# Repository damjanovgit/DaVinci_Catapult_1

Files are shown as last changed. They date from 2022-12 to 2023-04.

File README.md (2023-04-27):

# DaVinci_Catapult_1

This project is done as practical part of subjects Computer electronics and Microcontroller systems in academic 2022/23 year, winter semester. 
For realisation, we had to design PCB with all components that we need to control stepper motors, which are used to position the catapult, then limit switches and lasers, and the final result, our catapult, is shown on picture below.
<p align="center">


## Connection instructions

### PCB power supply

First, we need to connect 12V supply to PCB, and we use proto-board as voltage source to input pins of LM317. Black wire is connected to the ground, and red one to +12V. (Note: on this proto-board is written that it gives +15V but in reality it is +12V voltage source, so it is recommended to always check all sources with multimeter).
<p align="center">


 ### Connecting Picket3 programmer to PCB
 
 For programming microcontroller we use Picket3 programmer, and it has 5 wires that need to be connected in proper way. At the pictures bellow we have shown Picket3 pinout and its connection to PCB.
 <p align="center">
 
 

 ### Stepper motor and laser connection
 Six stepper motors were used to operate the catapult. Of that number, two stepper motors are used to move the lasers, the remaining four are on the catapult itself.
 Connectors for stepper motors are marked with numbers 1, 2, 3 and 4 and they need to be placed as it is shown on the picture.
 Two connectors that are next to these are used for lasers, and it is important that whichever laser we connect next to connector 4 is considered as upper laser(goes on the left side of catapult).
 <p align="center">
 
 
 Power supply for lasers is connected as it is shown on next picture, wires for every laser go in pairs (+ -, + -). Next to this we connect limit switches(next 4 pins).
 
  <p align="center">
 
 
 ### Connecting to a computer
 
 For this, we use USB to UART converter that allows us to connect a device with a UART interface to a computer via a USB port.
  <p align="center">
 
 
When everything is propperly connected, it is necessary to enable the programming of the microcontroller on the board, and after this has been successfully completed, we can control the catapult. Controlling the catapult and lasers is done by entering appropriate characters into the serial communication terminal. The table below represents the commands with the corresponding characters and description.

| Command | Functionality |
| :---: | :---: |
| a | Laser 1 left rotation |
| d | Laser 1 right rotation |
| s | Stop laser 1 rotation |
| j | Laser 2 left rotation |
| l | Laser 2 right rotation |
| k | Stop laser 2 rotation |
| c | Calibration |
| f | Launch |
| p | Positioning of the catapult |
| b | Rotate catapult left |
| m | Rotate catapult right |
| n | Stop rotating |
| z | Tension management |
| u | Tension management |
| i | Firing |
| o | Firing |

Using the commands a, d, j and l we control the lasers by turning them left or right until we aim at the target. When the laser rays are intersected, it means that the target is aimed, and we stop their movement with the s and k commands. Once we have determined the position of the target, we use the p command to position the catapult so that it is ready for launch. Then, use command f to fire a cannonball. Using the b, m, n, z, u, i, o commands, manual control of all other motors is enabled for testing purposes.

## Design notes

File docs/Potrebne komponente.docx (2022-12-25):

LATCH FOR DRIVING STEPPER MOTORS:

X8

-catalog (https://eu.mouser.com/c/semiconductors/logic-ics/encoders-decoders-multiplexers-demultiplexers/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):

https://eu.mouser.com/ProductDetail/onsemi/MC74HC175ADG?qs=qg33o%252B8vzFoIlG2G0iHepQ%3D%3D

-datasheet (https://eu.mouser.com/datasheet/2/308/MC74HC175A_D-1811422.pdf)

DECODER 3/8

-catalog

https://eu.mouser.com/c/semiconductors/logic-ics/encoders-decoders-multiplexers-demultiplexers/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

-part

https://eu.mouser.com/ProductDetail/Texas-Instruments/SN74HCS237QDRQ1?qs=81r%252BiQLm7BRJlAHNZgIr4g%3D%3D

ULN2003

-part

https://eu.mouser.com/ProductDetail/STMicroelectronics/ULN2003D1013TR?qs=YnPipOpXm6FQ98RZGZk5Pg%3D%3D

CRYSTAL OSCILATOR

-catalog:

https://eu.mouser.com/c/passive-components/frequency-control-timing-devices/crystals/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

-potencijalno I ovaj

https://eu.mouser.com/ProductDetail/Wurth-Elektronik/830003151?qs=2WXlatMagcHisY7XHApyYg%3D%3D

-datasheet (https://eu.mouser.com/datasheet/2/445/830003156B-2005241.pdf)

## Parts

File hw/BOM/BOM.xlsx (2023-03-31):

Item | Qty | Reference(s) | Value | Mouser Part No. | Link to Mouser
1 | 1 | XTAL/S | 830003156B | 710-830003156B | https://eu.mouser.com/ProductDetail/Wurth-Elektronik/830003156B?qs=2WXlatMagcHnVMrUSWOG9g%3D%3D
2 | 1 | C7 | 10uF | 80-C0805C106K8R7210 | https://eu.mouser.com/ProductDetail/KEMET/C0805C106K8RAC7210?qs=qDynDzKJm89Noj94vfKrew%3D%3D
3 | 13 | C1, C2, C3,C5, C9, C12, C13, C14, C15, C16, C17, C18, C19 | 0.1uF | 80-C0805C104K5RACLR | https://eu.mouser.com/ProductDetail/KEMET/C0805C104K5RAC7411
4 | 1 | C20 | 100uF | 581-CM21X5R107M06AT | https://eu.mouser.com/ProductDetail/KYOCERA-AVX/CM21X5R107M06AT
5 | 1 | C4 | 1u | 80-C0805C105Z4V | https://eu.mouser.com/ProductDetail/KEMET/C0805C105Z4VACTU?qs=XSafd0xJmRINotKjOdb5hw%3D%3D
6 | 4 | C6, C8, C10, C11 | 47pF | 80-C0805C470J5GACLR | https://eu.mouser.com/ProductDetail/KEMET/C0805C470J5GAC7210?qs=wYAydIdPQphRIc65nI7ifw%3D%3D
7 | 1 | R3 | 240 | 603-RT0805BRD07240R | https://eu.mouser.com/ProductDetail/YAGEO/RT0805BRD07240RL?qs=aZCcseWLxnuOXuRNghjaKA%3D%3D
8 | 1 | R2 | 220 | 603-RT0805BRD07220RL | https://eu.mouser.com/ProductDetail/YAGEO/RT0805BRD07220RL?qs=%2Ff7pOCXLR5ctU4g2ONNN1A%3D%3D
9 | 2 | R11, R12 | 27 | 603-RT0805FRE0727RL | https://eu.mouser.com/ProductDetail/YAGEO/RT0805FRE0727RL?qs=4CyHz7GXqSiza0HQqKGx2Q%3D%3D
10 | 1 | R4 | 390 | 603-RT0805FRE07390RL | https://eu.mouser.com/ProductDetail/YAGEO/RT0805FRE07390RL?qs=%2FgLOArm3Wr4KJrVuTb07CQ%3D%3D
11 | 1 | IC2 | 317EMP | 863-LM317MADTRKG | https://eu.mouser.com/ProductDetail/onsemi/LM317MADTRKG?qs=2OtswVQKCOFlhMcZfF6npw%3D%3D
12 | 1 | IC1 |  | 579-PIC24FJ64GA002TI | https://eu.mouser.com/ProductDetail/Microchip-Technology/PIC24FJ64GA002T-I-SS?qs=Fllw7YelV393P08MHz84Bg%3D%3D
13 | 4 | IC9, IC10, IC11, IC12 | ULN2003D1013TR | 595-ULN2003AIDR | https://eu.mouser.com/ProductDetail/Texas-Instruments/ULN2003AIDR?qs=pbofycSusePLfAeFJ8tqkg%3D%3D
14 | 1 | IC13 | FT230XS-U | 895-FT230XS-U | https://eu.mouser.com/ProductDetail/FTDI/FT230XS-U?qs=Gp1Yz1mis3UZolxbXux7lw%3D%3D
15 | 6 | IC3, IC4, IC5, IC6, IC7, IC8 | MC74HC175ADG | 863-MC74HC175ADG | https://eu.mouser.com/ProductDetail/onsemi/MC74HC175ADG?qs=qg33o%252B8vzFoIlG2G0iHepQ%3D%3D
16 | 1 | U1 | Decoder/Demultiplexer | 771-74HC237D-Q100J | https://eu.mouser.com/ProductDetail/Nexperia/74HC237D-Q100J?qs=cbprxTG2Yq9x2EcO4aYbZA%3D%3D
17 | 1 | J1 | UJ2-BH-1-TH | 490-UJ2-BH-W2-TH | https://eu.mouser.com/ProductDetail/CUI-Devices/UJ2-BH-W2-TH?qs=5mqXD9RfOg2S8wXYHZgk9A%3D%3D
18 | 2 | PGEC_GP, PROG_VDD |  | 571-5-146280-3 | https://eu.mouser.com/ProductDetail/TE-Connectivity/5-146280-3?qs=bwpFY26eRVf7xnwkMZzVxA%3D%3D
19 | 10 | I2C_SPI, J8, J9, MOTOR1, MOTOR2, MOTOR3, MOTOR4, MOTOR5, MOTOR6, PROGRAMATOR |  | 649-68000-105HTLF | https://eu.mouser.com/ProductDetail/Amphenol-FCI/68000-105HTLF?qs=w%2Fv1CP2dgqrYgNyQVoiqDw%3D%3D
20 | 8 | R1, R5, R6, R7, R8, R9, R10, R13 | 10k | 603-RT0805BRD0710KL | https://eu.mouser.com/ProductDetail/YAGEO/RT0805BRD0710KL?qs=87%2Fgv35YuOdOfU%252BBkLDVxA%3D%3D
21 | 1 | GND PIN
22 | 1 | VDD PIN

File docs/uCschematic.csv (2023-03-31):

Part | Value | Device | Package | Description | ARROW_PART_NUMBER | ARROW_PRICE-STOCK | AVAILABILITY | DESCRIPTION | HEIGHT | MANUFACTURER_NAME | MANUFACTURER_PART_NUMBER | MF | MOUSER_PART_NUMBER | MOUSER_PRICE-STOCK | MOUSER_TESTING_PART_NUMBER | MOUSER_TESTING_PRICE-STOCK | MP | MPN | OC_FARNELL | OC_NEWARK | PACKAGE | POPULARITY | PRICE | PURCHASE-URL | SPICEMODEL | SPICEPREFIX
C1 | 100nF | C | C0805 | CAPACITOR, European symbol |  |  |  |  |  |  |  |  |  |  |  |  |  |  |  |  |  |  |  |  | NONE | C
C2 | 100nF | C | C0805 | CAPACITOR, European symbol |  |  |  |  |  |  |  |  |  |  |  |  |  |  |  |  |  |  |  |  | NONE | C
C3 | 100nF | C | C0805 | CAPACITOR, European symbol |  |  |  |  |  |  |  |  |  |  |  |  |  |  |  |  |  |  |  |  | NONE | C
C4 | 1u | C | C0805 | CAPACITOR, European symbol |  |  |  |  |  |  |  |  |  |  |  |  |  |  |  |  |  |  |  |  | NONE | C
C5 | 0.1u | C | C0805 | CAPACITOR, European symbol |  |  |  |  |  |  |  |  |  |  |  |  |  |  |  |  |  |  |  |  | NONE | C
C6 | 47pF | C | C0805 | CAPACITOR, European symbol |  |  |  |  |  |  |  |  |  |  |  |  |  |  |  |  |  |  |  |  | NONE | C
C7 | 10uF | C | C0805 | CAPACITOR, European symbol |  |  |  |  |  |  |  |  |  |  |  |  |  |  |  |  |  |  |  |  | NONE | C
C8 | 47pF | C | C0805 | CAPACITOR, European symbol |  |  |  |  |  |  |  |  |  |  |  |  |  |  |  |  |  |  |  |  | NONE | C
C9 | 0.1u | C | C0805 | CAPACITOR, European symbol |  |  |  |  |  |  |  |  |  |  |  |  |  |  |  |  |  |  |  |  | NONE | C
C10 | 47pF | C | C0805 | CAPACITOR, European symbol |  |  |  |  |  |  |  |  |  |  |  |  |  |  |  |  |  |  |  |  | NONE | C
C11 | 47pF | C | C0805 | CAPACITOR, European symbol |  |  |  |  |  |  |  |  |  |  |  |  |  |  |  |  |  |  |  |  | NONE | C
C12 | 0.1u | C | C0805 | CAPACITOR, European symbol |  |  |  |  |  |  |  |  |  |  |  |  |  |  |  |  |  |  |  |  | NONE | C
C13 | 0.1u | C | C0805 | CAPACITOR, European symbol |  |  |  |  |  |  |  |  |  |  |  |  |  |  |  |  |  |  |  |  | NONE | C
C14 | 0.1u | C | C0805 | CAPACITOR, European symbol |  |  |  |  |  |  |  |  |  |  |  |  |  |  |  |  |  |  |  |  | NONE | C
C15 | 0.1u | C | C0805 | CAPACITOR, European symbol |  |  |  |  |  |  |  |  |  |  |  |  |  |  |  |  |  |  |  |  | NONE | C
C16 | 0.1u | C | C0805 | CAPACITOR, European symbol |  |  |  |  |  |  |  |  |  |  |  |  |  |  |  |  |  |  |  |  | NONE | C
C17 | 0.1u | C | C0805 | CAPACITOR, European symbol |  |  |  |  |  |  |  |  |  |  |  |  |  |  |  |  |  |  |  |  | NONE | C
C18 | 0.1u | C | C0805 | CAPACITOR, European symbol |  |  |  |  |  |  |  |  |  |  |  |  |  |  |  |  |  |  |  |  | NONE | C
C19 | 0.1u | C | C0805 | CAPACITOR, European symbol |  |  |  |  |  |  |  |  |  |  |  |  |  |  |  |  |  |  |  |  | NONE | C
CAT_ANGLE | PIN1-2 | PIN1-2 | 62221 | CONN TAB FASTON BRASS .187 PCB |  |  |  |  |  |  |  | TYCO ELECTRONICS |  |  |  |  |  | 62221-1 | unknown | 16H2318
CAT_ROTATION | PIN1-2 | PIN1-2 | 62221 | CONN TAB FASTON BRASS .187 PCB |  |  |  |  |  |  |  | TYCO ELECTRONICS |  |  |  |  |  | 62221-1 | unknown | 16H2318
CS | PIN1-2 | PIN1-2 | 62221 | CONN TAB FASTON BRASS .187 PCB |  |  |  |  |  |  |  | TYCO ELECTRONICS |  |  |  |  |  | 62221-1 | unknown | 16H2318
GND | PIN1-2 | PIN1-2 | 62221 | CONN TAB FASTON BRASS .187 PCB |  |  |  |  |  |  |  | TYCO ELECTRONICS |  |  |  |  |  | 62221-1 | unknown | 16H2318
GND1 | PIN1-2 | PIN1-2 | 62221 | CONN TAB FASTON BRASS .187 PCB |  |  |  |  |  |  |  | TYCO ELECTRONICS |  |  |  |  |  | 62221-1 | unknown | 16H2318
GND_CAT_ANGLE | PIN1-2 | PIN1-2 | 62221 | CONN TAB FASTON BRASS .187 PCB |  |  |  |  |  |  |  | TYCO ELECTRONICS |  |  |  |  |  | 62221-1 | unknown | 16H2318
GND_CAT_ROTATION | PIN1-2 | PIN1-2 | 62221 | CONN TAB FASTON BRASS .187 PCB |  |  |  |  |  |  |  | TYCO ELECTRONICS |  |  |  |  |  | 62221-1 | unknown | 16H2318
GND_GP_1 | PIN1-2 | PIN1-2 | 62221 | CONN TAB FASTON BRASS .187 PCB |  |  |  |  |  |  |  | TYCO ELECTRONICS |  |  |  |  |  | 62221-1 | unknown | 16H2318
GND_GP_LASER1 | PIN1-2 | PIN1-2 | 62221 | CONN TAB FASTON BRASS .187 PCB |  |  |  |  |  |  |  | TYCO ELECTRONICS |  |  |  |  |  | 62221-1 | unknown | 16H2318
GND_GP_LASER2 | PIN1-2 | PIN1-2 | 62221 | CONN TAB FASTON BRASS .187 PCB |  |  |  |  |  |  |  | TYCO ELECTRONICS |  |  |  |  |  | 62221-1 | unknown | 16H2318
GND_SM1 | PIN1-2 | PIN1-2 | 62221 | CONN TAB FASTON BRASS .187 PCB |  |  |  |  |  |  |  | TYCO ELECTRONICS |  |  |  |  |  | 62221-1 | unknown | 16H2318
GND_SM2 | PIN1-2 | PIN1-2 | 62221 | CONN TAB FASTON BRASS .187 PCB |  |  |  |  |  |  |  | TYCO ELECTRONICS |  |  |  |  |  | 62221-1 | unknown | 16H2318
GND_SM3 | PIN1-2 | PIN1-2 | 62221 | CONN TAB FASTON BRASS .187 PCB |  |  |  |  |  |  |  | TYCO ELECTRONICS |  |  |  |  |  | 62221-1 | unknown | 16H2318
GND_SM4 | PIN1-2 | PIN1-2 | 62221 | CONN TAB FASTON BRASS .187 PCB |  |  |  |  |  |  |  | TYCO ELECTRONICS |  |  |  |  |  | 62221-1 | unknown | 16H2318
GND_SM5 | PIN1-2 | PIN1-2 | 62221 | CONN TAB FASTON BRASS .187 PCB |  |  |  |  |  |  |  | TYCO ELECTRONICS |  |  |  |  |  | 62221-1 | unknown | 16H2318
GND_SM6 | PIN1-2 | PIN1-2 | 62221 | CONN TAB FASTON BRASS .187 PCB |  |  |  |  |  |  |  | TYCO ELECTRONICS |  |  |  |  |  | 62221-1 | unknown | 16H2318
GND_SPI/I2C | PIN1-2 | PIN1-2 | 62221 | CONN TAB FASTON BRASS .187 PCB |  |  |  |  |  |  |  | TYCO ELECTRONICS |  |  |  |  |  | 62221-1 | unknown | 16H2318
GP | PIN1-2 | PIN1-2 | 62221 | CONN TAB FASTON BRASS .187 PCB |  |  |  |  |  |  |  | TYCO ELECTRONICS |  |  |  |  |  | 62221-1 | unknown | 16H2318
GP_1 | PIN1-2 | PIN1-2 | 62221 | CONN TAB FASTON BRASS .187 PCB |  |  |  |  |  |  |  | TYCO ELECTRONICS |  |  |  |  |  | 62221-1 | unknown | 16H2318
GP_LASER1 | PIN1-2 | PIN1-2 | 62221 | CONN TAB FASTON BRASS .187 PCB |  |  |  |  |  |  |  | TYCO ELECTRONICS |  |  |  |  |  | 62221-1 | unknown | 16H2318
GP_LASER2 | PIN1-2 | PIN1-2 | 62221 | CONN TAB FASTON BRASS .187 PCB |  |  |  |  |  |  |  | TYCO ELECTRONICS |  |  |  |  |  | 62221-1 | unknown | 16H2318
IC1 | PIC24FJXXGA002/SO | PIC24FJXXGA002/SO | SO28W | PIC24FJxxGA002
IC2 | 317EMP | 317EMP | SOT223 | Positive VOLTAGE REGULATOR
IC3 | MC74HC175ADG | MC74HC175ADG | SOIC127P600X175-16N | ON Semiconductor MC74HC175ADG, D Type Flip Flop, LSTTL, 2 6 V, 16-Pin SOIC |  |  |  | ON Semiconductor MC74HC175ADG, D Type Flip Flop, LSTTL, 2 6 V, 16-Pin SOIC | 1.75mm | onsemi | MC74HC175ADG |  | 863-MC74HC175ADG | https://www.mouser.co.uk/ProductDetail/onsemi/MC74HC175ADG?qs=qg33o%252B8vzFoIlG2G0iHepQ%3D%3D
IC4 | MC74HC175ADG | MC74HC175ADG | SOIC127P600X175-16N | ON Semiconductor MC74HC175ADG, D Type Flip Flop, LSTTL, 2 6 V, 16-Pin SOIC |  |  |  | ON Semiconductor MC74HC175ADG, D Type Flip Flop, LSTTL, 2 6 V, 16-Pin SOIC | 1.75mm | onsemi | MC74HC175ADG |  | 863-MC74HC175ADG | https://www.mouser.co.uk/ProductDetail/onsemi/MC74HC175ADG?qs=qg33o%252B8vzFoIlG2G0iHepQ%3D%3D
IC5 | MC74HC175ADG | MC74HC175ADG | SOIC127P600X175-16N | ON Semiconductor MC74HC175ADG, D Type Flip Flop, LSTTL, 2 6 V, 16-Pin SOIC |  |  |  | ON Semiconductor MC74HC175ADG, D Type Flip Flop, LSTTL, 2 6 V, 16-Pin SOIC | 1.75mm | onsemi | MC74HC175ADG |  | 863-MC74HC175ADG | https://www.mouser.co.uk/ProductDetail/onsemi/MC74HC175ADG?qs=qg33o%252B8vzFoIlG2G0iHepQ%3D%3D
IC6 | MC74HC175ADG | MC74HC175ADG | SOIC127P600X175-16N | ON Semiconductor MC74HC175ADG, D Type Flip Flop, LSTTL, 2 6 V, 16-Pin SOIC |  |  |  | ON Semiconductor MC74HC175ADG, D Type Flip Flop, LSTTL, 2 6 V, 16-Pin SOIC | 1.75mm | onsemi | MC74HC175ADG |  | 863-MC74HC175ADG | https://www.mouser.co.uk/ProductDetail/onsemi/MC74HC175ADG?qs=qg33o%252B8vzFoIlG2G0iHepQ%3D%3D
IC7 | MC74HC175ADG | MC74HC175ADG | SOIC127P600X175-16N | ON Semiconductor MC74HC175ADG, D Type Flip Flop, LSTTL, 2 6 V, 16-Pin SOIC |  |  |  | ON Semiconductor MC74HC175ADG, D Type Flip Flop, LSTTL, 2 6 V, 16-Pin SOIC | 1.75mm | onsemi | MC74HC175ADG |  | 863-MC74HC175ADG | https://www.mouser.co.uk/ProductDetail/onsemi/MC74HC175ADG?qs=qg33o%252B8vzFoIlG2G0iHepQ%3D%3D
IC8 | MC74HC175ADG | MC74HC175ADG | SOIC127P600X175-16N | ON Semiconductor MC74HC175ADG, D Type Flip Flop, LSTTL, 2 6 V, 16-Pin SOIC |  |  |  | ON Semiconductor MC74HC175ADG, D Type Flip Flop, LSTTL, 2 6 V, 16-Pin SOIC | 1.75mm | onsemi | MC74HC175ADG |  | 863-MC74HC175ADG | https://www.mouser.co.uk/ProductDetail/onsemi/MC74HC175ADG?qs=qg33o%252B8vzFoIlG2G0iHepQ%3D%3D
IC9 | ULN2003D1013TR | ULN2003D1013TR | SOIC127P600X175-16N | ULN2003D1013TR, Darlington Transistor Array, NPN 0.5A 50V, Array 7 HFE:1000, 16-Pin, SO |  |  |  | ULN2003D1013TR, Darlington Transistor Array, NPN 0.5A 50V, Array 7 HFE:1000, 16-Pin, SO | 1.75mm | STMicroelectronics | ULN2003D1013TR |  | 511-ULN2003D1013TR | https://www.mouser.co.uk/ProductDetail/STMicroelectronics/ULN2003D1013TR?qs=YnPipOpXm6FQ98RZGZk5Pg%3D%3D
IC10 | ULN2003D1013TR | ULN2003D1013TR | SOIC127P600X175-16N | ULN2003D1013TR, Darlington Transistor Array, NPN 0.5A 50V, Array 7 HFE:1000, 16-Pin, SO |  |  |  | ULN2003D1013TR, Darlington Transistor Array, NPN 0.5A 50V, Array 7 HFE:1000, 16-Pin, SO | 1.75mm | STMicroelectronics | ULN2003D1013TR |  | 511-ULN2003D1013TR | https://www.mouser.co.uk/ProductDetail/STMicroelectronics/ULN2003D1013TR?qs=YnPipOpXm6FQ98RZGZk5Pg%3D%3D
IC11 | ULN2003D1013TR | ULN2003D1013TR | SOIC127P600X175-16N | ULN2003D1013TR, Darlington Transistor Array, NPN 0.5A 50V, Array 7 HFE:1000, 16-Pin, SO |  |  |  | ULN2003D1013TR, Darlington Transistor Array, NPN 0.5A 50V, Array 7 HFE:1000, 16-Pin, SO | 1.75mm | STMicroelectronics | ULN2003D1013TR |  | 511-ULN2003D1013TR | https://www.mouser.co.uk/ProductDetail/STMicroelectronics/ULN2003D1013TR?qs=YnPipOpXm6FQ98RZGZk5Pg%3D%3D
IC12 | ULN2003D1013TR | ULN2003D1013TR | SOIC127P600X175-16N | ULN2003D1013TR, Darlington Transistor Array, NPN 0.5A 50V, Array 7 HFE:1000, 16-Pin, SO |  |  |  | ULN2003D1013TR, Darlington Transistor Array, NPN 0.5A 50V, Array 7 HFE:1000, 16-Pin, SO | 1.75mm | STMicroelectronics | ULN2003D1013TR |  | 511-ULN2003D1013TR | https://www.mouser.co.uk/ProductDetail/STMicroelectronics/ULN2003D1013TR?qs=YnPipOpXm6FQ98RZGZk5Pg%3D%3D
IC13 | FT230XS-U | FT230XS-U | SOP64P599X175-16N | USB Interface IC USB to Basic Serial UART IC SSOP-16 | FT230XS-U | https://www.arrow.com/en/products/ft230xs-u/ftdi-chip |  | USB Interface IC USB to Basic Serial UART IC SSOP-16 | 1.753mm | FTDI Chip | FT230XS-U |  | 895-FT230XS-U | https://www.mouser.co.uk/ProductDetail/FTDI/FT230XS-U?qs=Gp1Yz1mis3UZolxbXux7lw%3D%3D
J1 | USB3075-30-A | USB3075-30-A | USB307530A | GCT (GLOBAL CONNECTOR TECHNOLOGY) - USB3075-30-A - USB Connector, Micro USB Type B, USB 2.0, Receptacle, 5 Ways, Surface Mount, Right Angle |  |  |  | GCT (GLOBAL CONNECTOR TECHNOLOGY) - USB3075-30-A - USB Connector, Micro USB Type B, USB 2.0, Receptacle, 5 Ways, Surface Mount, Right Angle | 2.7mm | GCT (GLOBAL CONNECTOR TECHNOLOGY) | USB3075-30-A |  | 640-USB3075-30-A | https://www.mouser.co.uk/ProductDetail/GCT/USB3075-30-A?qs=KUoIvG%2F9IlbGMJplbp1ybA%3D%3D
MCLR | PIN1-2 | PIN1-2 | 62221 | CONN TAB FASTON BRASS .187 PCB |  |  |  |  |  |  |  | TYCO ELECTRONICS |  |  |  |  |  | 62221-1 | unknown | 16H2318
MISO | PIN1-2 | PIN1-2 | 62221 | CONN TAB FASTON BRASS .187 PCB |  |  |  |  |  |  |  | TYCO ELECTRONICS |  |  |  |  |  | 62221-1 | unknown | 16H2318
PGEC | PIN1-2 | PIN1-2 | 62221 | CONN TAB FASTON BRASS .187 PCB |  |  |  |  |  |  |  | TYCO ELECTRONICS |  |  |  |  |  | 62221-1 | unknown | 16H2318
PGEC/GP | PIN1-2 | PIN1-2 | 62221 | CONN TAB FASTON BRASS .187 PCB |  |  |  |  |  |  |  | TYCO ELECTRONICS |  |  |  |  |  | 62221-1 | unknown | 16H2318
PGEC_PROG | PIN1-2 | PIN1-2 | 62221 | CONN TAB FASTON BRASS .187 PCB |  |  |  |  |  |  |  | TYCO ELECTRONICS |  |  |  |  |  | 62221-1 | unknown | 16H2318
PGED | PIN1-2 | PIN1-2 | 62221 | CONN TAB FASTON BRASS .187 PCB |  |  |  |  |  |  |  | TYCO ELECTRONICS |  |  |  |  |  | 62221-1 | unknown | 16H2318
Q1 |  | XTAL/S | QS | CRYSTAL |  |  |  |  |  |  |  |  |  |  |  |  |  |  |  |  |  | 59
R1 | 10k | R | R0805 | RESISTOR, European symbol |  |  |  |  |  |  |  |  |  |  |  |  |  |  |  |  |  |  |  |  | NONE | R
R2 | 220 | R | R0805 | RESISTOR, European symbol |  |  |  |  |  |  |  |  |  |  |  |  |  |  |  |  |  |  |  |  | NONE | R
R3 | 240 | R | R0805 | RESISTOR, European symbol |  |  |  |  |  |  |  |  |  |  |  |  |  |  |  |  |  |  |  |  | NONE | R
R4 | 390 | R | R0805 | RESISTOR, European symbol |  |  |  |  |  |  |  |  |  |  |  |  |  |  |  |  |  |  |  |  | NONE | R
R5 | 10k | R | R0805 | RESISTOR, European symbol |  |  |  |  |  |  |  |  |  |  |  |  |  |  |  |  |  |  |  |  | NONE | R
R6 | 10k | R | R0805 | RESISTOR, European symbol |  |  |  |  |  |  |  |  |  |  |  |  |  |  |  |  |  |  |  |  | NONE | R
R7 | 10k | R | R0805 | RESISTOR, European symbol |  |  |  |  |  |  |  |  |  |  |  |  |  |  |  |  |  |  |  |  | NONE | R
R8 | 10k | R | R0805 | RESISTOR, European symbol |  |  |  |  |  |  |  |  |  |  |  |  |  |  |  |  |  |  |  |  | NONE | R
R9 | 10k | R | R0805 | RESISTOR, European symbol |  |  |  |  |  |  |  |  |  |  |  |  |  |  |  |  |  |  |  |  | NONE | R
R10 | 10k | R | R0805 | RESISTOR, European symbol |  |  |  |  |  |  |  |  |  |  |  |  |  |  |  |  |  |  |  |  | NONE | R
R11 | 27 | R-EU_R0805 | R0805 | RESISTOR, European symbol |  |  |  |  |  |  |  |  |  |  |  |  |  |  |  |  |  | 86 |  |  |  | R
R12 | 27 | R-EU_R0805 | R0805 | RESISTOR, European symbol |  |  |  |  |  |  |  |  |  |  |  |  |  |  |  |  |  | 86 |  |  |  | R
SCLK/SCL | PIN1-2 | PIN1-2 | 62221 | CONN TAB FASTON BRASS .187 PCB |  |  |  |  |  |  |  | TYCO ELECTRONICS |  |  |  |  |  | 62221-1 | unknown | 16H2318
SDA/MOSI | PIN1-2 | PIN1-2 | 62221 | CONN TAB FASTON BRASS .187 PCB |  |  |  |  |  |  |  | TYCO ELECTRONICS |  |  |  |  |  | 62221-1 | unknown | 16H2318
SM11 | PIN1-2 | PIN1-2 | 62221 | CONN TAB FASTON BRASS .187 PCB |  |  |  |  |  |  |  | TYCO ELECTRONICS |  |  |  |  |  | 62221-1 | unknown | 16H2318
SM12 | PIN1-2 | PIN1-2 | 62221 | CONN TAB FASTON BRASS .187 PCB |  |  |  |  |  |  |  | TYCO ELECTRONICS |  |  |  |  |  | 62221-1 | unknown | 16H2318
SM13 | PIN1-2 | PIN1-2 | 62221 | CONN TAB FASTON BRASS .187 PCB |  |  |  |  |  |  |  | TYCO ELECTRONICS |  |  |  |  |  | 62221-1 | unknown | 16H2318
SM14 | PIN1-2 | PIN1-2 | 62221 | CONN TAB FASTON BRASS .187 PCB |  |  |  |  |  |  |  | TYCO ELECTRONICS |  |  |  |  |  | 62221-1 | unknown | 16H2318
SM21 | PIN1-2 | PIN1-2 | 62221 | CONN TAB FASTON BRASS .187 PCB |  |  |  |  |  |  |  | TYCO ELECTRONICS |  |  |  |  |  | 62221-1 | unknown | 16H2318
SM22 | PIN1-2 | PIN1-2 | 62221 | CONN TAB FASTON BRASS .187 PCB |  |  |  |  |  |  |  | TYCO ELECTRONICS |  |  |  |  |  | 62221-1 | unknown | 16H2318
SM23 | PIN1-2 | PIN1-2 | 62221 | CONN TAB FASTON BRASS .187 PCB |  |  |  |  |  |  |  | TYCO ELECTRONICS |  |  |  |  |  | 62221-1 | unknown | 16H2318
SM24 | PIN1-2 | PIN1-2 | 62221 | CONN TAB FASTON BRASS .187 PCB |  |  |  |  |  |  |  | TYCO ELECTRONICS |  |  |  |  |  | 62221-1 | unknown | 16H2318
SM31 | PIN1-2 | PIN1-2 | 62221 | CONN TAB FASTON BRASS .187 PCB |  |  |  |  |  |  |  | TYCO ELECTRONICS |  |  |  |  |  | 62221-1 | unknown | 16H2318
SM32 | PIN1-2 | PIN1-2 | 62221 | CONN TAB FASTON BRASS .187 PCB |  |  |  |  |  |  |  | TYCO ELECTRONICS |  |  |  |  |  | 62221-1 | unknown | 16H2318
SM33 | PIN1-2 | PIN1-2 | 62221 | CONN TAB FASTON BRASS .187 PCB |  |  |  |  |  |  |  | TYCO ELECTRONICS |  |  |  |  |  | 62221-1 | unknown | 16H2318
SM34 | PIN1-2 | PIN1-2 | 62221 | CONN TAB FASTON BRASS .187 PCB |  |  |  |  |  |  |  | TYCO ELECTRONICS |  |  |  |  |  | 62221-1 | unknown | 16H2318
SM41 | PIN1-2 | PIN1-2 | 62221 | CONN TAB FASTON BRASS .187 PCB |  |  |  |  |  |  |  | TYCO ELECTRONICS |  |  |  |  |  | 62221-1 | unknown | 16H2318
SM42 | PIN1-2 | PIN1-2 | 62221 | CONN TAB FASTON BRASS .187 PCB |  |  |  |  |  |  |  | TYCO ELECTRONICS |  |  |  |  |  | 62221-1 | unknown | 16H2318
SM43 | PIN1-2 | PIN1-2 | 62221 | CONN TAB FASTON BRASS .187 PCB |  |  |  |  |  |  |  | TYCO ELECTRONICS |  |  |  |  |  | 62221-1 | unknown | 16H2318
SM44 | PIN1-2 | PIN1-2 | 62221 | CONN TAB FASTON BRASS .187 PCB |  |  |  |  |  |  |  | TYCO ELECTRONICS |  |  |  |  |  | 62221-1 | unknown | 16H2318
SM51 | PIN1-2 | PIN1-2 | 62221 | CONN TAB FASTON BRASS .187 PCB |  |  |  |  |  |  |  | TYCO ELECTRONICS |  |  |  |  |  | 62221-1 | unknown | 16H2318
SM52 | PIN1-2 | PIN1-2 | 62221 | CONN TAB FASTON BRASS .187 PCB |  |  |  |  |  |  |  | TYCO ELECTRONICS |  |  |  |  |  | 62221-1 | unknown | 16H2318
SM53 | PIN1-2 | PIN1-2 | 62221 | CONN TAB FASTON BRASS .187 PCB |  |  |  |  |  |  |  | TYCO ELECTRONICS |  |  |  |  |  | 62221-1 | unknown | 16H2318
SM54 | PIN1-2 | PIN1-2 | 62221 | CONN TAB FASTON BRASS .187 PCB |  |  |  |  |  |  |  | TYCO ELECTRONICS |  |  |  |  |  | 62221-1 | unknown | 16H2318
SM61 | PIN1-2 | PIN1-2 | 62221 | CONN TAB FASTON BRASS .187 PCB |  |  |  |  |  |  |  | TYCO ELECTRONICS |  |  |  |  |  | 62221-1 | unknown | 16H2318
SM62 | PIN1-2 | PIN1-2 | 62221 | CONN TAB FASTON BRASS .187 PCB |  |  |  |  |  |  |  | TYCO ELECTRONICS |  |  |  |  |  | 62221-1 | unknown | 16H2318
SM63 | PIN1-2 | PIN1-2 | 62221 | CONN TAB FASTON BRASS .187 PCB |  |  |  |  |  |  |  | TYCO ELECTRONICS |  |  |  |  |  | 62221-1 | unknown | 16H2318
SM64 | PIN1-2 | PIN1-2 | 62221 | CONN TAB FASTON BRASS .187 PCB |  |  |  |  |  |  |  | TYCO ELECTRONICS |  |  |  |  |  | 62221-1 | unknown | 16H2318
U1 | 74HC237D-Q100J | 74HC237D-Q100J | SOIC127P600X175-16N | None Check availability |  |  | In Stock | Decoder/Demultiplexer 1 x 3:8 16-SO |  |  |  | Nexperia USA Inc. |  |  |  |  | 74HC237D-Q100J |  |  |  | SOIC-16 Nexperia USA |  | None | https://pricing.snapeda.com/search/part/74HC237D-Q100J/?ref=eda
VDD | 12V | PIN1-2 | 62221 | CONN TAB FASTON BRASS .187 PCB |  |  |  |  |  |  |  | TYCO ELECTRONICS |  |  |  |  |  | 62221-1 | unknown | 16H2318
VDD_3.3 | PIN1-2 | PIN1-2 | 62221 | CONN TAB FASTON BRASS .187 PCB |  |  |  |  |  |  |  | TYCO ELECTRONICS |  |  |  |  |  | 62221-1 | unknown | 16H2318
VDD_PROG | PIN1-2 | PIN1-2 | 62221 | CONN TAB FASTON BRASS .187 PCB |  |  |  |  |  |  |  | TYCO ELECTRONICS |  |  |  |  |  | 62221-1 | unknown | 16H2318
VDD_PROG1 | PIN1-2 | PIN1-2 | 62221 | CONN TAB FASTON BRASS .187 PCB |  |  |  |  |  |  |  | TYCO ELECTRONICS |  |  |  |  |  | 62221-1 | unknown | 16H2318
VDD_UC | PIN1-2 | PIN1-2 | 62221 | CONN TAB FASTON BRASS .187 PCB |  |  |  |  |  |  |  | TYCO ELECTRONICS |  |  |  |  |  | 62221-1 | unknown | 16H2318

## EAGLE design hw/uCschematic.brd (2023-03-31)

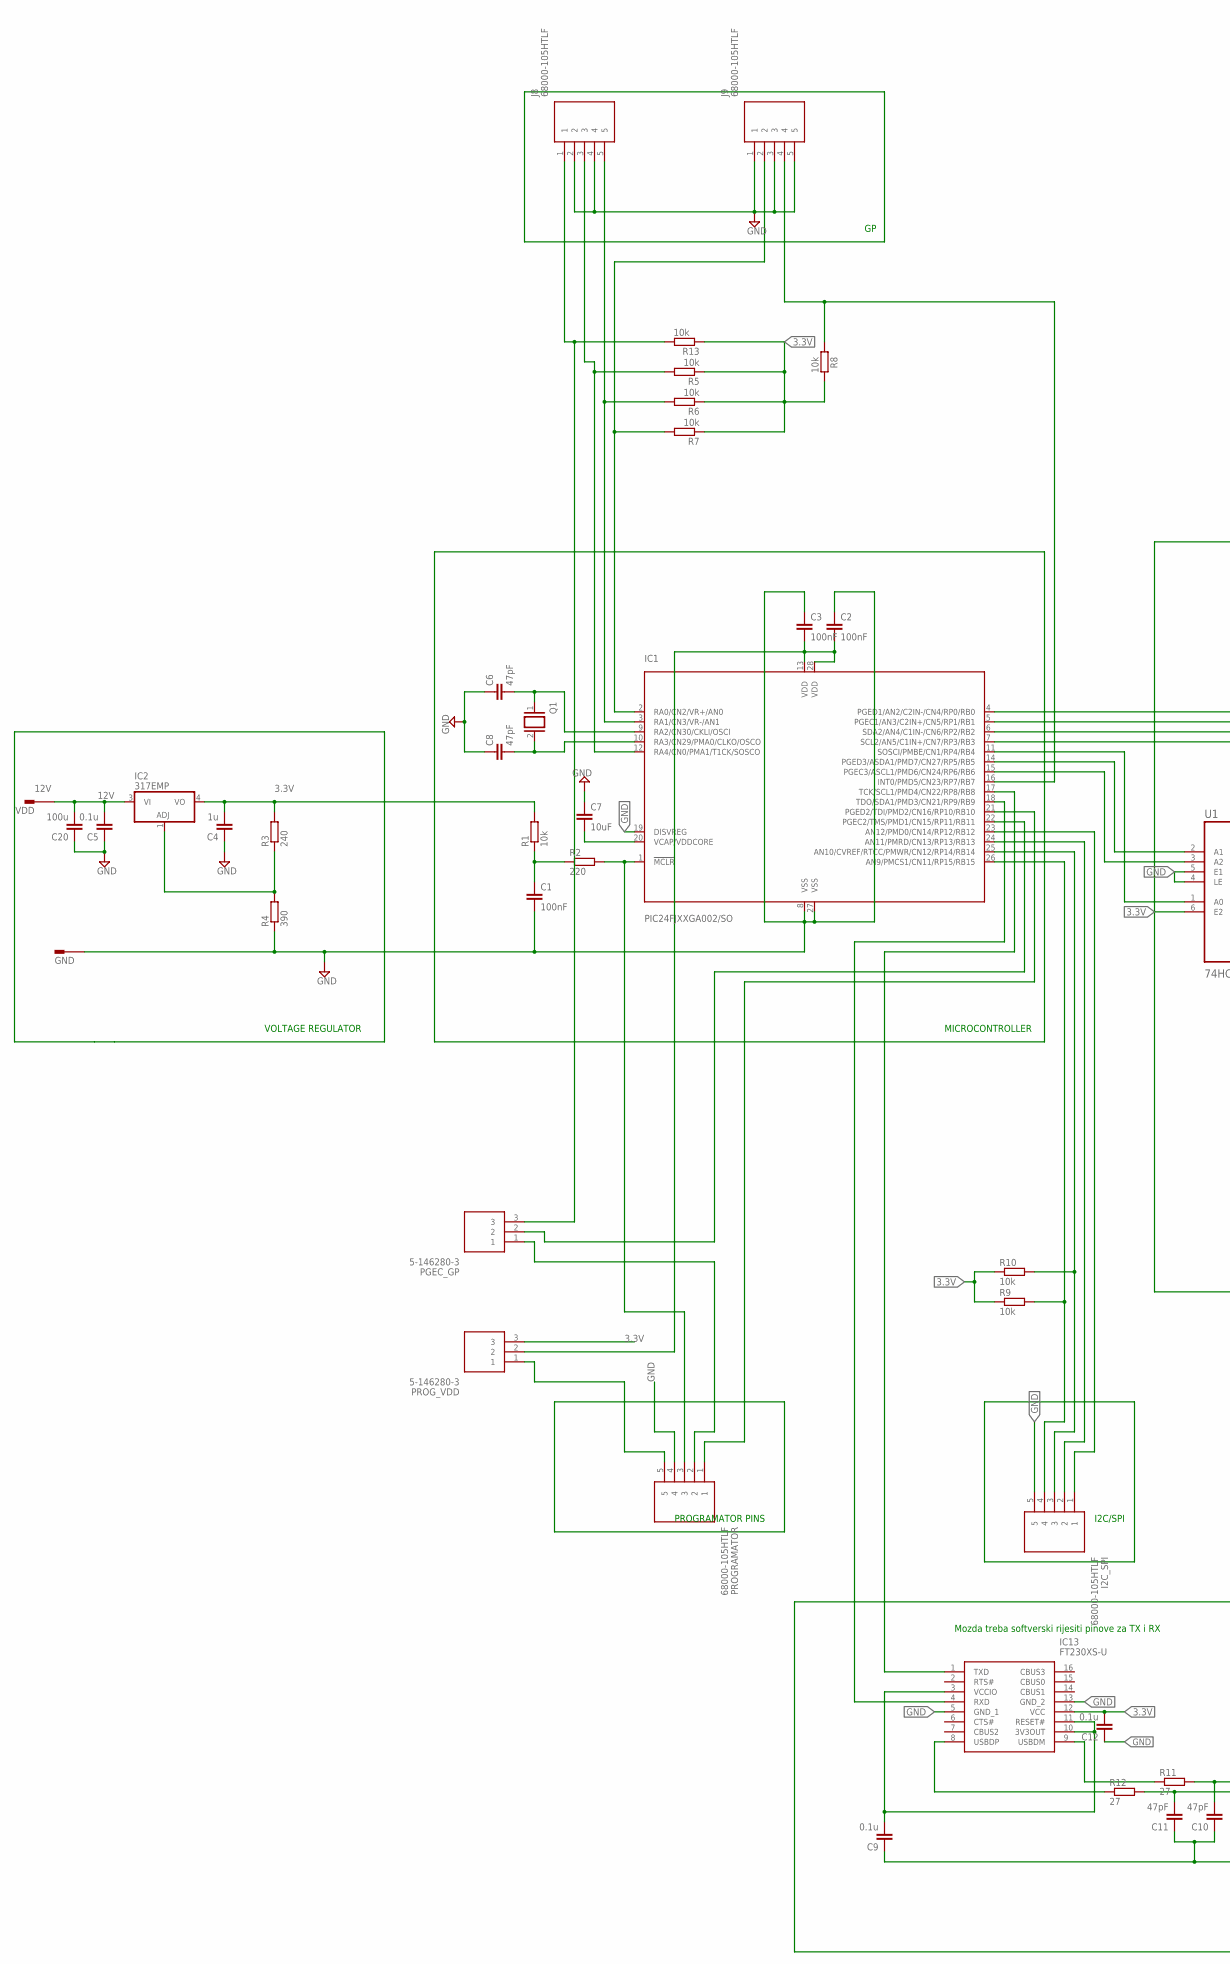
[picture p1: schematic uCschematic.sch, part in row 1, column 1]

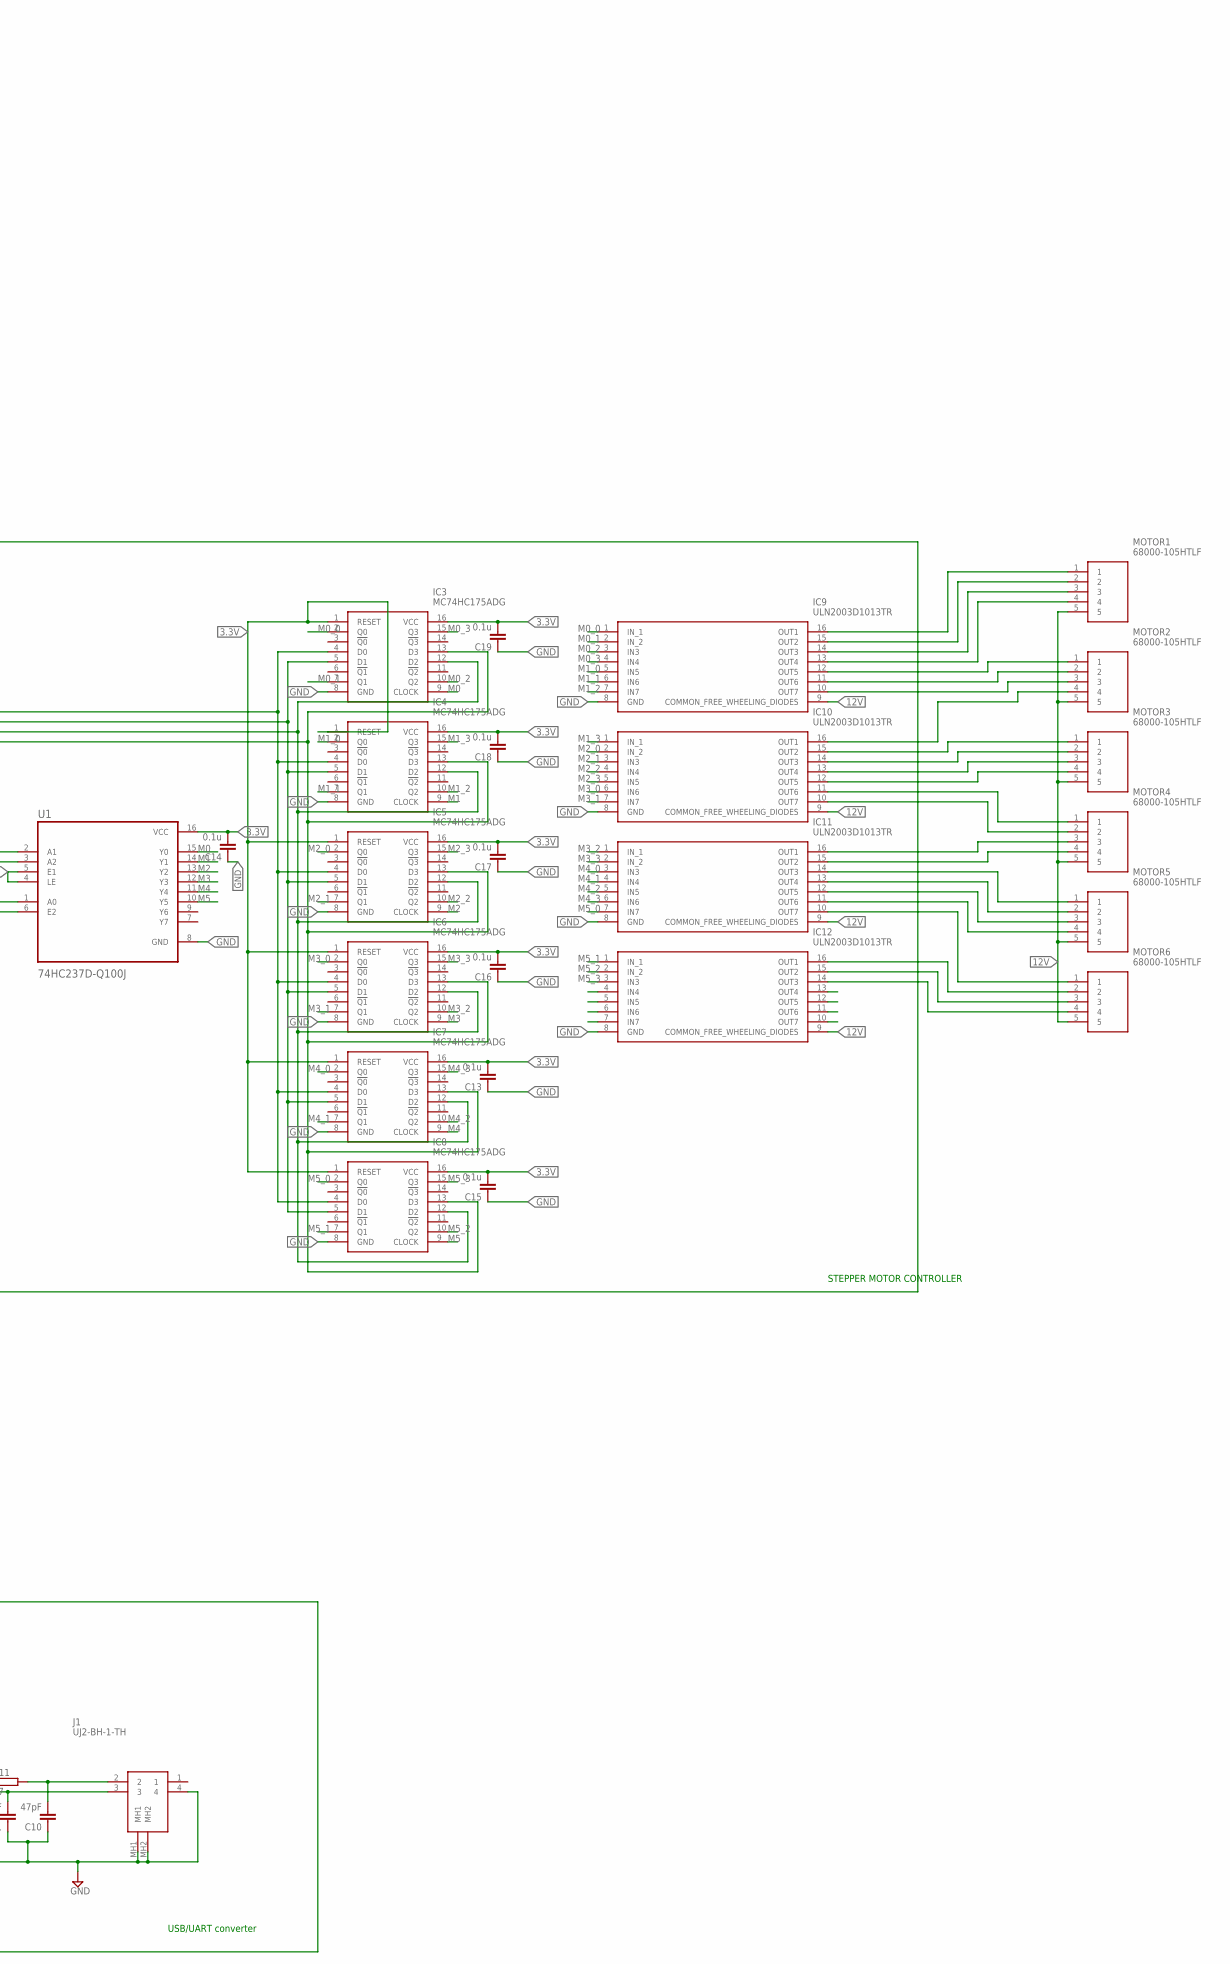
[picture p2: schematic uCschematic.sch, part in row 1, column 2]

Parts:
C1, C2, C3: 100nF; C0805
C4: 1u; C0805
C5, C9, C12, C13, C14, C15, C16, C17, C18, C19: 0.1u; C0805
C6, C8, C10, C11: 47pF; C0805
C7: 10uF; C0805
C20: 100u; C0805
GND: PIN1-2; 62221
I2C_SPI: 68000-105HTLF; HDRV5W67P0X254_1X5_1270X241X85
IC1: PIC24FJXXGA002/SO; SO28W
IC2: 317EMP; SOT223
IC3, IC4, IC5, IC6, IC7, IC8: MC74HC175ADG; SOIC127P600X175-16N
IC9, IC10, IC11, IC12: ULN2003D1013TR; SOIC127P600X175-16N
IC13: FT230XS-U; SOP64P599X175-16N
J1: UJ2-BH-1-TH; UJ2BH1TH
J8, J9: 68000-105HTLF; HDRV5W67P0X254_1X5_1270X241X85
MOTOR1, MOTOR2, MOTOR3, MOTOR4, MOTOR5, MOTOR6: 68000-105HTLF; HDRV5W67P0X254_1X5_1270X241X85
PGEC_GP: 5-146280-3; HDRV3W97P0X254_1X3_721X234X821
PROGRAMATOR: 68000-105HTLF; HDRV5W67P0X254_1X5_1270X241X85
PROG_VDD: 5-146280-3; HDRV3W97P0X254_1X3_721X234X821
Q1: XTAL/S; QS
R1, R5, R6, R7, R8, R9, R10, R13: 10k; R0805
R2: 220; R0805
R3: 240; R0805
R4: 390; R0805
R11, R12: 27; R0805
U1: 74HC237D-Q100J; SOIC127P600X175-16N
VDD: 12V; 62221

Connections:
3.3V: C4.2, C12.2, C13.2, C14.2, C15.2, C16.2, C17.2, C18.2, C19.2, IC2.4 (VO), IC3.1 (RESET), IC3.16 (VCC), IC4.1 (RESET), IC4.16 (VCC), IC5.1 (RESET), IC5.16 (VCC), IC6.1 (RESET), IC6.16 (VCC), IC7.1 (RESET), IC7.16 (VCC), IC8.1 (RESET), IC8.16 (VCC), IC13.12 (VCC), PROG_VDD.3, R1.2, R3.2, R5.1, R6.1, R7.1, R8.2, R9.1, R10.1, R13.1, U1.6 (E2), U1.16 (VCC)
12V: C5.2, C20.2, IC2.3 (VI), IC9.9 (COMMON_FREE_WHEELING_DIODES), IC10.9 (COMMON_FREE_WHEELING_DIODES), IC11.9 (COMMON_FREE_WHEELING_DIODES), IC12.9 (COMMON_FREE_WHEELING_DIODES), MOTOR1.5, MOTOR2.5, MOTOR3.5, MOTOR4.5, MOTOR5.5, MOTOR6.5, VDD.1
GND: C1.2, C2.1, C3.1, C4.1, C5.1, C6.1, C7.1, C8.1, C9.1, C10.1, C11.1, C12.1, C14.1, C20.1, GND.1, I2C_SPI.5, IC1.8 (VSS), IC1.19 (DISVREG), IC1.27 (VSS), IC3.8 (GND), IC4.8 (GND), IC5.8 (GND), IC6.8 (GND), IC7.8 (GND), IC8.8 (GND), IC9.8 (GND), IC10.8 (GND), IC11.8 (GND), IC12.8 (GND), IC13.5 (GND_1), IC13.13 (GND_2), J1.4, J1.MH1, J1.MH2, J8.2, J8.4, J9.1, J9.3, J9.5, PROGRAMATOR.4, R4.1, U1.4 (LE), U1.5 (E1), U1.8 (GND)
GP_OKIDAC: J8.1, PGEC_GP.3, R13.2
M0: IC3.9 (CLOCK), U1.15 (Y0)
M0_0: IC3.2 (Q0), IC9.1 (IN_1)
M0_1: IC3.7 (Q1), IC9.2 (IN_2)
M0_2: IC3.10 (Q2), IC9.3 (IN3)
M0_3: IC3.15 (Q3), IC9.4 (IN4)
M1: IC4.9 (CLOCK), U1.14 (Y1)
M1_0: IC4.2 (Q0), IC9.5 (IN5)
M1_1: IC4.7 (Q1), IC9.6 (IN6)
M1_2: IC4.10 (Q2), IC9.7 (IN7)
M1_3: IC4.15 (Q3), IC10.1 (IN_1)
M2: IC5.9 (CLOCK), U1.13 (Y2)
M2_0: IC5.2 (Q0), IC10.2 (IN_2)
M2_1: IC5.7 (Q1), IC10.3 (IN3)
M2_2: IC5.10 (Q2), IC10.4 (IN4)
M2_3: IC5.15 (Q3), IC10.5 (IN5)
M3: IC6.9 (CLOCK), U1.12 (Y3)
M3_0: IC6.2 (Q0), IC10.6 (IN6)
M3_1: IC6.7 (Q1), IC10.7 (IN7)
M3_2: IC6.10 (Q2), IC11.1 (IN_1)
M3_3: IC6.15 (Q3), IC11.2 (IN_2)
M4: IC7.9 (CLOCK), U1.11 (Y4)
M4_0: IC7.2 (Q0), IC11.3 (IN3)
M4_1: IC7.7 (Q1), IC11.4 (IN4)
M4_2: IC7.10 (Q2), IC11.5 (IN5)
M4_3: IC7.15 (Q3), IC11.6 (IN6)
M5: IC8.9 (CLOCK), U1.10 (Y5)
M5_0: IC8.2 (Q0), IC11.7 (IN7)
M5_1: IC8.7 (Q1), IC12.1 (IN_1)
M5_2: IC8.10 (Q2), IC12.2 (IN_2)
M5_3: IC8.15 (Q3), IC12.3 (IN3)
unnamed: C1.1, R1.1, R2.1
unnamed: IC1.1 (!MCLR), PROGRAMATOR.3, R2.2
unnamed: C7.2, IC1.20 (VCAP/VDDCORE)
unnamed: C2.2, C3.2, IC1.13 (VDD), IC1.28 (VDD), PROG_VDD.2
unnamed: C6.2, IC1.9 (RA2/CN30/CKLI/OSCI), Q1.1
unnamed: IC1.21 (PGED2/TDI/PMD2/CN16/RP10/RB10), PROGRAMATOR.1
unnamed: C8.2, IC1.10 (RA3/CN29/PMA0/CLKO/OSCO), Q1.2
unnamed: IC2.1 (ADJ), R3.1, R4.2
unnamed: IC1.7 (SCL2/AN5/C1IN+/CN7/RP3/RB3), IC3.13 (D3), IC4.13 (D3), IC5.13 (D3), IC6.13 (D3), IC7.13 (D3), IC8.13 (D3)
unnamed: IC1.6 (SDA2/AN4/C1IN-/CN6/RP2/RB2), IC3.12 (D2), IC4.12 (D2), IC5.12 (D2), IC6.12 (D2), IC7.12 (D2), IC8.12 (D2)
unnamed: IC1.11 (SOSCI/PMBE/CN1/RP4/RB4), U1.1 (A0)
unnamed: IC1.14 (PGED3/ASDA1/PMD7/CN27/RP5/RB5), U1.2 (A1)
unnamed: IC1.15 (PGEC3/ASCL1/PMD6/CN24/RP6/RB6), U1.3 (A2)
unnamed: IC1.12 (RA4/CN0/PMA1/T1CK/SOSCO), J8.3, R5.2
unnamed: IC1.5 (PGEC1/AN3/C2IN+/CN5/RP1/RB1), IC3.5 (D1), IC4.5 (D1), IC5.5 (D1), IC6.5 (D1), IC7.5 (D1), IC8.5 (D1)
unnamed: IC1.4 (PGED1/AN2/C2IN-/CN4/RP0/RB0), IC3.4 (D0), IC4.4 (D0), IC5.4 (D0), IC6.4 (D0), IC7.4 (D0), IC8.4 (D0)
unnamed: IC1.22 (PGEC2/TMS/PMD1/CN15/RP11/RB11), PGEC_GP.2
unnamed: IC1.18 (TDO/SDA1/PMD3/CN21/RP9/RB9), IC13.4 (RXD)
unnamed: IC1.17 (TCK/SCL1/PMD4/CN22/RP8/RB8), IC13.1 (TXD)
unnamed: PROGRAMATOR.5, PROG_VDD.1
unnamed: PGEC_GP.1, PROGRAMATOR.2
unnamed: IC1.3 (RA1/CN3/VR-/AN1), J8.5, R6.2
unnamed: IC9.16 (OUT1), MOTOR1.1
unnamed: IC9.15 (OUT2), MOTOR1.2
unnamed: IC9.14 (OUT3), MOTOR1.3
unnamed: IC9.13 (OUT4), MOTOR1.4
unnamed: IC9.12 (OUT5), MOTOR2.1
unnamed: IC9.11 (OUT6), MOTOR2.2
unnamed: IC9.10 (OUT7), MOTOR2.3
unnamed: IC1.2 (RA0/CN2/VR+/AN0), J9.2, R7.2
unnamed: IC1.16 (INT0/PMD5/CN23/RP7/RB7), J9.4, R8.1
unnamed: I2C_SPI.1, IC1.23 (AN12/PMD0/CN14/RP12/RB12)
unnamed: I2C_SPI.2, IC1.24 (AN11/PMRD/CN13/RP13/RB13)
unnamed: I2C_SPI.3, IC1.25 (AN10/CVREF/RTCC/PMWR/CN12/RP14/RB14), R10.2
unnamed: I2C_SPI.4, IC1.26 (AN9/PMCS1/CN11/RP15/RB15), R9.2
unnamed: C10.2, J1.2, R11.2
unnamed: IC10.16 (OUT1), MOTOR2.4
unnamed: IC10.15 (OUT2), MOTOR3.1
unnamed: IC10.14 (OUT3), MOTOR3.2
unnamed: IC10.13 (OUT4), MOTOR3.3
unnamed: IC10.12 (OUT5), MOTOR3.4
unnamed: IC10.11 (OUT6), MOTOR4.1
unnamed: IC10.10 (OUT7), MOTOR4.2
unnamed: C9.2, IC13.3 (VCCIO), IC13.10 (3V3OUT), IC13.11 (RESET#)
unnamed: C11.2, J1.3, R12.2
unnamed: IC13.9 (USBDM), R11.1
unnamed: IC13.8 (USBDP), R12.1
unnamed: IC12.15 (OUT2), MOTOR6.3
unnamed: IC11.16 (OUT1), MOTOR4.3
unnamed: IC11.15 (OUT2), MOTOR4.4
unnamed: IC11.14 (OUT3), MOTOR5.1
unnamed: IC11.13 (OUT4), MOTOR5.2
unnamed: IC11.12 (OUT5), MOTOR5.3
unnamed: IC11.11 (OUT6), MOTOR5.4
unnamed: IC11.10 (OUT7), MOTOR6.1
unnamed: IC12.16 (OUT1), MOTOR6.2
unnamed: IC12.14 (OUT3), MOTOR6.4

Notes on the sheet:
VOLTAGE REGULATOR
MICROCONTROLLER
STEPPER MOTOR CONTROLLER
PROGRAMATOR PINS
I2C/SPI
Mozda treba softverski rijesiti pinove za TX i RX
USB/UART converter

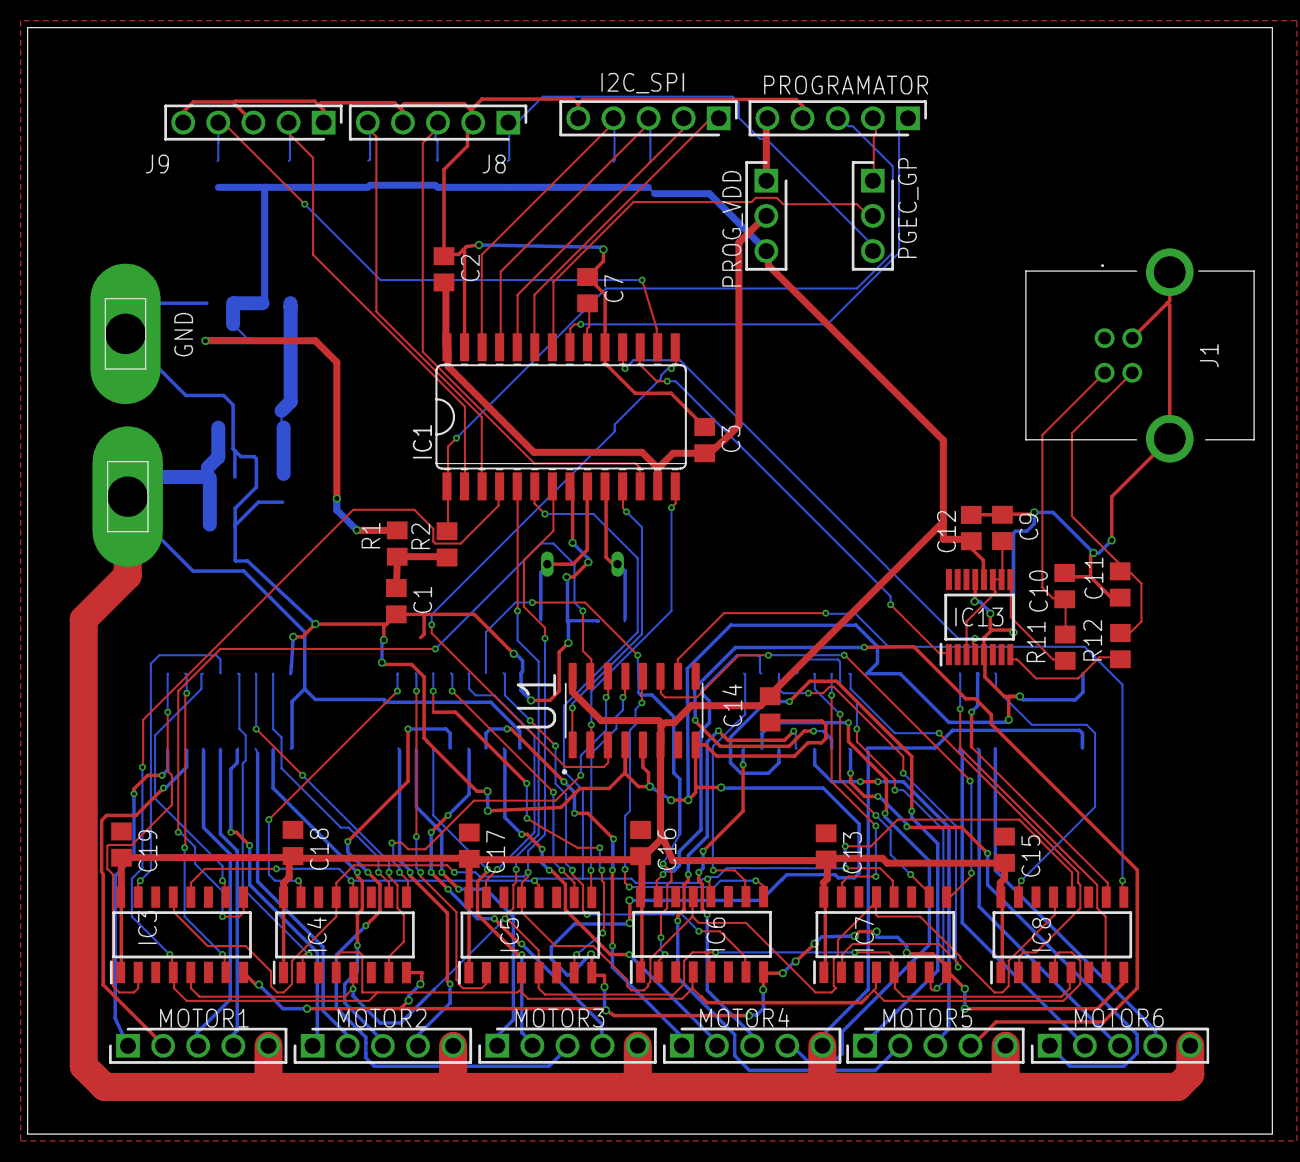
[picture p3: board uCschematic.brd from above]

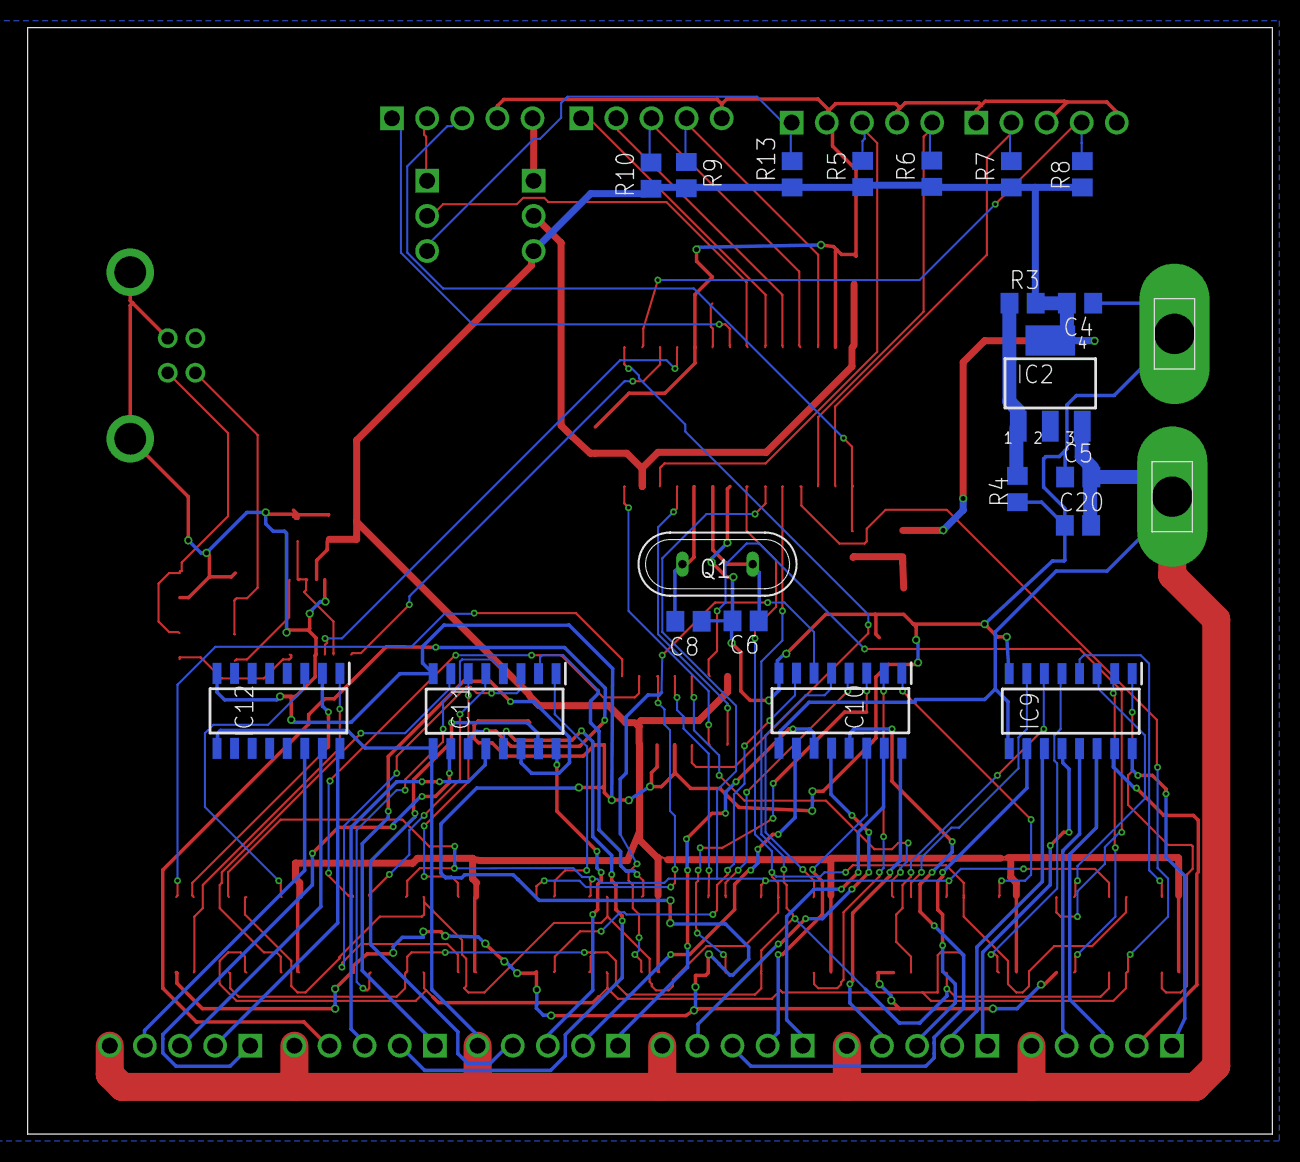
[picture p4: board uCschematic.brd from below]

Board: 2 copper layers, 90.0 x 80.0 mm, 63 parts (20 on the bottom side), 91 nets.

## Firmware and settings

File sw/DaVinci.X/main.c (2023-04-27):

/**
  Generated main.c file from MPLAB Code Configurator

  @Company
    Microchip Technology Inc.

  @File Name
    main.c

  @Summary
    This is the generated main.c using PIC24 / dsPIC33 / PIC32MM MCUs.

  @Description
    This source file provides main entry point for system initialization and application code development.
    Generation Information :
        Product Revision  :  PIC24 / dsPIC33 / PIC32MM MCUs - 1.171.1
        Device            :  PIC24FJ64GA702
    The generated drivers are tested against the following:
        Compiler          :  XC16 v1.70
        MPLAB 	          :  MPLAB X v5.50
 */

/*
    (c) 2020 Microchip Technology Inc. and its subsidiaries. You may use this
    software and any derivatives exclusively with Microchip products.

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
    IN NO EVENT WILL MICROCHIP BE LIABLE FOR ANY INDIRECT, SPECIAL, PUNITIVE,
    INCIDENTAL OR CONSEQUENTIAL LOSS, DAMAGE, COST OR EXPENSE OF ANY KIND
    WHATSOEVER RELATED TO THE SOFTWARE, HOWEVER CAUSED, EVEN IF MICROCHIP HAS
    BEEN ADVISED OF THE POSSIBILITY OR THE DAMAGES ARE FORESEEABLE. TO THE
    FULLEST EXTENT ALLOWED BY LAW, MICROCHIP'S TOTAL LIABILITY ON ALL CLAIMS IN
    ANY WAY RELATED TO THIS SOFTWARE WILL NOT EXCEED THE AMOUNT OF FEES, IF ANY,
    THAT YOU HAVE PAID DIRECTLY TO MICROCHIP FOR THIS SOFTWARE.

    MICROCHIP PROVIDES THIS SOFTWARE CONDITIONALLY UPON YOUR ACCEPTANCE OF THESE
    TERMS.
 */

/**
  Section: Included Files
 */
#define FCY 4000000UL
#include "mcc_generated_files/system.h"
#include "mcc_generated_files/uart1.h"
#include "xc.h"
#include "coordinate.h"
#include <libpic30.h>
#include "mcc_generated_files/pin_manager.h"
#include <stdio.h>



#define IDLE     7<<4
#define YAW      0    // rotate catapult
#define PITCH    1<<4 // up/down catapult
#define TIGHT    2<<4 // tighten catapult
#define FIRE     3<<4 // fire
#define LASER1   4<<4 // laser 1 motor
#define LASER2   5<<4 // laser 2 motor

#define CATAPULT_YAW_RATIO   0.11f
#define CATAPULT_PITCH_RATIO 0.2f
#define TIGHTENING_RATIO     0.3f // 1/30

// Vo of flying object meters per second
int speed = 10;

// rotations of the motors
uint8_t RIGHT[] ={1,3,2,6,4,12,8,9};
uint8_t LEFT[] ={9,8,12,4,6,2,3,1};
// command received
volatile uint8_t command = 0;

#ifdef LUT
double LUT_TIGHT[] ={0.6, 0.73, 0.87, 1.22, 1.57, 1.8};


static double calculate_tight_angle(double distance){
    if(distance < 0.6){
        return LUT_TIGHT[0]; 
    }
    else if(distance >=0.6 && distance < 0.75){
        return LUT_TIGHT[1];
    }
    else if(distance >=0.75 && distance < 1.0){
        return LUT_TIGHT[2];
    }
    else if(distance >=1.0 && distance < 1.2){
        return LUT_TIGHT[3];
    }
    else if(distance >=1.2 && distance < 1.5){
        return LUT_TIGHT[4];
    }
    else if(distance >=1.5 && distance < 2){
        return LUT_TIGHT[5];
    }
    else{
        return LUT_TIGHT[6];
    }
}
#else
static double calculate_tight_angle(double distance){
    double trsh= 2.0;
    double result;
    result = 0.75*distance +0.25;
    if(result >trsh)
        result = trsh;
    else if(result <0.5)
        result = 0.5;
    return result;
}
#endif
// functions for turning motors
static inline void turn(int motor, uint8_t side[8]) {
    static int step = 0;
    step = step % 8;
    LATB = IDLE | side[step];
    __delay_us(500);
    LATB = motor | side[step];
    __delay_us(500);
    LATB = IDLE;
    step++;
}
void turn_left(int motor) {
    turn(motor, LEFT);
}

void turn_right(int motor) {
    turn(motor, RIGHT);
}

int calculate_steps(float angle,float ratio)
{
    int steps = (int)(angle/(0.001522*ratio));
    return steps;
}

static inline void turn_for_given_angle(int motor, float angle, float ratio) {
    int steps = calculate_steps(angle, ratio);
    int step = 0;
    if(steps < 0)   // lower half of coordinate system
    {
        steps *= -1;
        for (int i = 0; i < steps; i++) {
            step = step % 8;
            LATB = IDLE | RIGHT[step];
            __delay_us(500);
            LATB = motor | RIGHT[step];
            __delay_us(500);
            LATB = IDLE;
            step++;
        }
    }
    else    // upper half of coordinate system
    {
        for (int i = 0; i < steps; i++) {
            step = step % 8;
            LATB = IDLE | LEFT[step];
            __delay_us(500);
            LATB = motor | LEFT[step];
            __delay_us(500);
            LATB = IDLE;
            step++;
        }
        
    }
    LATB = IDLE;
    __delay_us(500);
    LATB = motor | 0;
    __delay_us(500);
    LATB = IDLE;
}

void update_angle(int16_t steps,float ratio, float * angle)
{
    *angle = *angle + steps*0.001522*ratio;
}

static inline void calibrate_pitch()
{
    while(GP2_GetValue() == 1)
    {
        turn_right(PITCH);
    }
    LATB = IDLE;
    __delay_us(500);
    LATB = PITCH | 0;
    __delay_us(500);
    LATB = IDLE;
}

static inline void calibrate_fire()
{
    while(GP3_GetValue() == 1)
    {
        turn_right(FIRE);
    }
    turn_for_given_angle(FIRE,2.3,1);
    while(GP3_GetValue() == 1)
    {
        turn_right(FIRE);
    }
    LATB = IDLE;
    __delay_us(500);
    LATB = FIRE | 0;
    __delay_us(500);
    LATB = IDLE;
}


uint8_t tx_buffer[30] = "Da-Vinci is ready\n";

COORD laser1_coord = {.x = 0.0, .y =  0.2 };
COORD laser2_coord = {.x = 0.0, .y = -0.2 };
COORD target_coord = {.x = 0.0, .y =  0.0 };

float laser1_angle;
float laser2_angle;
float catapult_angle;
float pitch_angle;

/*
                         Main application
 */
int main(void) {
    // initialize the device
    SYSTEM_Initialize();
    GP2_SetDigitalInput();

    UART1_WriteBuffer(tx_buffer, 20);
    while (1) {
        switch (command) {
            case 'a': // laser 1 left rotation
            {
                turn_left(LASER1);
                update_angle(1,1, &laser1_angle);
                break;
            }
            case 'd': // laser 1 right rotation
            {
                turn_right(LASER1);
                update_angle(-1,1, &laser1_angle);
                break;
            }
            case 's': // stop laser 1 rotation
            {
                LATB = IDLE;
                __delay_us(500);
                LATB = LASER1 | 0;
                __delay_us(500);
                LATB = IDLE;
                command = 0;
                break;
            }
            case 'j': // laser 2 left rotation
            {
                turn_left(LASER2);
                update_angle(1,1, &laser2_angle);
                break;
            }
            case 'l': // laser 2 right rotation
            {
                turn_right(LASER2);
                update_angle(-1,1, &laser2_angle);
                break;
            }
            case 'k': // stop laser 2 rotation
            {
                LATB = IDLE;
                __delay_us(500);
                LATB = LASER2 | 0;
                __delay_us(500);
                LATB = IDLE;
                command = 0;
                break;
            }
            case 'c': // calibrate
            {
                /**
                 * Needs to write function for calibration
                 * @return 
                 */
                laser1_angle   = 0;
                laser2_angle   = 0;
                catapult_angle = 0;
                pitch_angle    = 3.1415/3;
                calibrate_pitch();
                calibrate_fire();
                command = 0;
                break;
            }
            case 'f': // fire
            {
                /**
                 * Needs to write function for firing
                 * @return 
                 */
                turn_for_given_angle(FIRE,2.3,1);
                command = 0;
                break;
            }
            case 'p': // position catapult
            {
                float catapult_angle_new;
                /*
                 * calculating target coordinates and writing it to target_coord
                 */
                calculate_target_coords(laser1_coord,laser1_angle,laser2_coord,laser2_angle,&target_coord);
                printf("%f\n",target_coord.x);
                printf("%f\n",target_coord.y);
                printf("%f\n", laser1_angle);
                printf("%f\n", laser2_angle);
                /*
                 * Calculating target position angle based on catapult coordinates (0,0)
                 * This means for what angle catapult needs to rotate
                 */
                catapult_angle_new = calculate_target_position_angle(target_coord);
                printf("%f",catapult_angle_new);
                /*
                 * This turns catapult for given angle written in catapult_angle
                 * This function also takes gear ratio of yaw mechanism
                 */
                turn_for_given_angle(YAW,catapult_angle_new - catapult_angle,CATAPULT_YAW_RATIO);
                catapult_angle = catapult_angle_new;    // after positioning update catapult angle
                /*
                 * This function calculates angle of firing
                 */
                calculate_angle(target_coord,speed,&pitch_angle);
                /*
                 * This function positions firing angle called pitch_angle
                 */
                turn_for_given_angle(PITCH,3.1415/3 - pitch_angle,CATAPULT_PITCH_RATIO);
                /**
                 * This function tighten catapult for firing
                 * 
                 */
                double tight_angle = calculate_tight_angle(calculate_distance(target_coord));
                turn_for_given_angle(TIGHT,tight_angle,TIGHTENING_RATIO);
                command = 0;
                break;
            }
            case 'b':
            {
                turn_left(YAW);
                break;
            }
            case 'm':
            {
                turn_right(YAW);
                break;
            }
            case 'n':
            {
                LATB = IDLE;
                __delay_us(500);
                LATB = YAW | 0;
                __delay_us(500);
                LATB = IDLE;
                command = 0;
                break;
            }
            case 'z':
            {
                turn_left(TIGHT);
                break;
            }
            case 'u':
            {
                turn_right(TIGHT);
                break;
            }
            case 'i':
            {
                turn_left(FIRE);
                break;
            }
            case 'o':
            {
                turn_right(FIRE);
                break;
            }
        }
    }
    return 1;
}

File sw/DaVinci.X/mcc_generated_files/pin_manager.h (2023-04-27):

/**
  PIN MANAGER Generated Driver File

  @Company:
    Microchip Technology Inc.

  @File Name:
    pin_manager.h

  @Summary:
    This is the generated manager file for the PIC24 / dsPIC33 / PIC32MM MCUs device.  This manager
    configures the pins direction, initial state, analog setting.
    The peripheral pin select, PPS, configuration is also handled by this manager.

  @Description:
    This source file provides implementations for PIN MANAGER.
    Generation Information :
        Product Revision  :  PIC24 / dsPIC33 / PIC32MM MCUs - 1.171.1
        Device            :  PIC24FJ64GA702
    The generated drivers are tested against the following:
        Compiler          :  XC16 v1.70
        MPLAB 	          :  MPLAB X v5.50
*/

/*
    (c) 2020 Microchip Technology Inc. and its subsidiaries. You may use this
    software and any derivatives exclusively with Microchip products.

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
    IN NO EVENT WILL MICROCHIP BE LIABLE FOR ANY INDIRECT, SPECIAL, PUNITIVE,
    INCIDENTAL OR CONSEQUENTIAL LOSS, DAMAGE, COST OR EXPENSE OF ANY KIND
    WHATSOEVER RELATED TO THE SOFTWARE, HOWEVER CAUSED, EVEN IF MICROCHIP HAS
    BEEN ADVISED OF THE POSSIBILITY OR THE DAMAGES ARE FORESEEABLE. TO THE
    FULLEST EXTENT ALLOWED BY LAW, MICROCHIP'S TOTAL LIABILITY ON ALL CLAIMS IN
    ANY WAY RELATED TO THIS SOFTWARE WILL NOT EXCEED THE AMOUNT OF FEES, IF ANY,
    THAT YOU HAVE PAID DIRECTLY TO MICROCHIP FOR THIS SOFTWARE.

    MICROCHIP PROVIDES THIS SOFTWARE CONDITIONALLY UPON YOUR ACCEPTANCE OF THESE
    TERMS.
*/

#ifndef _PIN_MANAGER_H
#define _PIN_MANAGER_H
/**
    Section: Includes
*/
#include <xc.h>

/**
    Section: Device Pin Macros
*/
/**
  @Summary
    Sets the GPIO pin, RA0, high using LATA0.

  @Description
    Sets the GPIO pin, RA0, high using LATA0.

  @Preconditions
    The RA0 must be set to an output.

  @Returns
    None.

  @Param
    None.

  @Example
    <code>
    // Set RA0 high (1)
    GP4_SetHigh();
    </code>

*/
#define GP4_SetHigh()          (_LATA0 = 1)
/**
  @Summary
    Sets the GPIO pin, RA0, low using LATA0.

  @Description
    Sets the GPIO pin, RA0, low using LATA0.

  @Preconditions
    The RA0 must be set to an output.

  @Returns
    None.

  @Param
    None.

  @Example
    <code>
    // Set RA0 low (0)
    GP4_SetLow();
    </code>

*/
#define GP4_SetLow()           (_LATA0 = 0)
/**
  @Summary
    Toggles the GPIO pin, RA0, using LATA0.

  @Description
    Toggles the GPIO pin, RA0, using LATA0.

  @Preconditions
    The RA0 must be set to an output.

  @Returns
    None.

  @Param
    None.

  @Example
    <code>
    // Toggle RA0
    GP4_Toggle();
    </code>

*/
#define GP4_Toggle()           (_LATA0 ^= 1)
/**
  @Summary
    Reads the value of the GPIO pin, RA0.

  @Description
    Reads the value of the GPIO pin, RA0.

  @Preconditions
    None.

  @Returns
    None.

  @Param
    None.

  @Example
    <code>
    uint16_t portValue;

    // Read RA0
    postValue = GP4_GetValue();
    </code>

*/
#define GP4_GetValue()         _RA0
/**
  @Summary
    Configures the GPIO pin, RA0, as an input.

  @Description
    Configures the GPIO pin, RA0, as an input.

  @Preconditions
    None.

  @Returns
    None.

  @Param
    None.

  @Example
    <code>
    // Sets the RA0 as an input
    GP4_SetDigitalInput();
    </code>

*/
#define GP4_SetDigitalInput()  (_TRISA0 = 1)
/**
  @Summary
    Configures the GPIO pin, RA0, as an output.

  @Description
    Configures the GPIO pin, RA0, as an output.

  @Preconditions
    None.

  @Returns
    None.

  @Param
    None.

  @Example
    <code>
    // Sets the RA0 as an output
    GP4_SetDigitalOutput();
    </code>

*/
#define GP4_SetDigitalOutput() (_TRISA0 = 0)
/**
  @Summary
    Sets the GPIO pin, RA1, high using LATA1.

  @Description
    Sets the GPIO pin, RA1, high using LATA1.

  @Preconditions
    The RA1 must be set to an output.

  @Returns
    None.

  @Param
    None.

  @Example
    <code>
    // Set RA1 high (1)
    GP3_SetHigh();
    </code>

*/
#define GP3_SetHigh()          (_LATA1 = 1)
/**
  @Summary
    Sets the GPIO pin, RA1, low using LATA1.

  @Description
    Sets the GPIO pin, RA1, low using LATA1.

  @Preconditions
    The RA1 must be set to an output.

  @Returns
    None.

  @Param
    None.

  @Example
    <code>
    // Set RA1 low (0)
    GP3_SetLow();
    </code>

*/
#define GP3_SetLow()           (_LATA1 = 0)
/**
  @Summary
    Toggles the GPIO pin, RA1, using LATA1.

  @Description
    Toggles the GPIO pin, RA1, using LATA1.

  @Preconditions
    The RA1 must be set to an output.

  @Returns
    None.

  @Param
    None.

  @Example
    <code>
    // Toggle RA1
    GP3_Toggle();
    </code>

*/
#define GP3_Toggle()           (_LATA1 ^= 1)
/**
  @Summary
    Reads the value of the GPIO pin, RA1.

  @Description
    Reads the value of the GPIO pin, RA1.

  @Preconditions
    None.

  @Returns
    None.

  @Param
    None.

  @Example
    <code>
    uint16_t portValue;

    // Read RA1
    postValue = GP3_GetValue();
    </code>

*/
#define GP3_GetValue()         _RA1
/**
  @Summary
    Configures the GPIO pin, RA1, as an input.

  @Description
    Configures the GPIO pin, RA1, as an input.

  @Preconditions
    None.

  @Returns
    None.

  @Param
    None.

  @Example
    <code>
    // Sets the RA1 as an input
    GP3_SetDigitalInput();
    </code>

*/
#define GP3_SetDigitalInput()  (_TRISA1 = 1)
/**
  @Summary
    Configures the GPIO pin, RA1, as an output.

  @Description
    Configures the GPIO pin, RA1, as an output.

  @Preconditions
    None.

  @Returns
    None.

  @Param
    None.

  @Example
    <code>
    // Sets the RA1 as an output
    GP3_SetDigitalOutput();
    </code>

*/
#define GP3_SetDigitalOutput() (_TRISA1 = 0)
/**
  @Summary
    Sets the GPIO pin, RA4, high using LATA4.

  @Description
    Sets the GPIO pin, RA4, high using LATA4.

  @Preconditions
    The RA4 must be set to an output.

  @Returns
    None.

  @Param
    None.

  @Example
    <code>
    // Set RA4 high (1)
    GP2_SetHigh();
    </code>

*/
#define GP2_SetHigh()          (_LATA4 = 1)
/**
  @Summary
    Sets the GPIO pin, RA4, low using LATA4.

  @Description
    Sets the GPIO pin, RA4, low using LATA4.

  @Preconditions
    The RA4 must be set to an output.

  @Returns
    None.

  @Param
    None.

  @Example
    <code>
    // Set RA4 low (0)
    GP2_SetLow();
    </code>

*/
#define GP2_SetLow()           (_LATA4 = 0)
/**
  @Summary
    Toggles the GPIO pin, RA4, using LATA4.

  @Description
    Toggles the GPIO pin, RA4, using LATA4.

  @Preconditions
    The RA4 must be set to an output.

  @Returns
    None.

  @Param
    None.

  @Example
    <code>
    // Toggle RA4
    GP2_Toggle();
    </code>
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

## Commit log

2022-12-25 Inital schema
    [uCboard.brd, uCschematic.sch]
2022-12-25 Made block for each component
    [uCschematic.sch]
2022-12-27 Sredjena sema
    [uCschematic.brd, uCschematic.sch]
2022-12-30 SPI, I2C, 4 granicna prekidaca, DONE
    [uCboard.brd, uCschematic.brd, uCschematic.sch]
2023-01-05 Uradjene izmjene PIN19 spojen na GND Kapacitivnost kondenzatora kod kristala kvarca je sada 47pF Dodana je masa za svaki od GP Dodana je masa za SPI i I2C Dodane su mase za koracne motore LATCH i ENA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
    [uCschematic.brd, uCschematic.sch]
2023-01-05 Dodana biblioteka za FT230XS-U UART/USB
2023-01-06 Uradjena sema za USB/UART converter
    [uCschematic.brd, uCschematic.sch]
2023-01-06 -Dodani bajpas kondenzatori.
    [uCschematic.brd, uCschematic.sch]
2023-01-06 -Unesene potrebne izmjene
    [uCschematic.brd, uCschematic.sch]
2023-01-06 Osiguravanje dodatnog GP u slucaju da bude potreban.
    [uCschematic.brd, uCschematic.sch]
2023-01-10 Šema u Proteusu za simulaciju rada step motora.
2023-01-10 Dodan csv file sa spiskom komponenata generisan pomoću Eagle-a
    [uCschematic.csv]
2023-01-11 Uradjena simulacija u proteusu USB micro AB -> USB type A Izvrsena simulacija u proteusu. Sve radi kako treba Izvrsene sitne izmjene na semi
    [uCschematic.brd, uCschematic.sch]
2023-01-22 Postavljene komponente na PCB, potrebno rutirati
    [copper_bottom.gbr, copper_top.gbr, drill_1_16.xln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]
2023-01-22 Postavljene komponente na PCB
2023-01-23 Dodan kondenzator većeg kapaciteta na ulazu za napajanje
    [uCschematic.brd, uCschematic.sch]
2023-01-24 - Rutiranje kontrolera za upravljanje stepper motorima - Dodavanje DRC fajla za dvoslojni PCB
    [uCschematic.brd]
2023-01-25 Rutiranje USB -a, graničnih prekidača i regulatora napona.
    [uCschematic.brd]
2023-01-25 Valjda gotovo
    [uCschematic.brd]
2023-02-01 PCB done
    [uCschematic.brd]
2023-02-01 Ispravke u rutiranju
    [uCschematic.brd]
2023-02-01 Addede drill and gerber files - check!
    [uCschematic.drl]
2023-02-02 Kreirani gerber, drill i BOM fajlovi
    [BOM.xlsx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]
2023-02-07 BOM file changed
    [BOM.xlsx]
2023-03-25 Renamed folder PCB to hw
    [BOM.xlsx, uCschematic.brd, uCschematic.csv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]
2023-03-29 Written function for calibration of pitch
2023-04-27 Impelented tightening function
